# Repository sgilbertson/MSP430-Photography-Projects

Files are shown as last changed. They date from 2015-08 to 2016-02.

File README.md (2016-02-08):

# MSP430-Photography-Projects
Personal MSP430 projects, mainly photography-related

Here will place source code for some of my personal MSP430 microcontroller projects, mainly related to photography.

They're not designed for general use, but if you're working with MSP430 processors perhaps you'll find some of the material helpful or interesting.

Pololu DRV8825 Adjustment
=========================

See [https://www.pololu.com/product/2133]

Procedure:
 * Install jumper pulling M0,M1,M2 all low, for full stepping, not micro-stepping
 * Do not connect a motor
 * Clip the red lead of a voltmeter to a small screwdriver
 * Clip the black lead to ground
 * Apply power
 * Adjust the trimpot on the DRV8825 until the voltmeter reads half the motor amps rating

For example, if the motor is rated for 1A, adjust until the meter reads 0.5V.

Sample Motors
-------------

These are some motors I found in nearby surplus stores.

Japan Servo KP35M2-035
 * 37 ohms
 * Internet sources suggest 500mA, implying 0.5*37=18.5V -- tune to 250mV
 * 1.8° per pulse (200 pulses per rev), but testing suggests 4x that -- 1Hz ~50 seconds per rev, 200H ~4rev/sec
 * Runs OK on 12V around 250mA
 * Wdg1 = blue/red, Wdg2 = white/yellow

Litton-Clifton Precision 11-SHBX-51KT H347
 * 16 Ohms
 * 0.312A -- tune to 161mV
 * 0.312*16=5V
 * 1.8° per pulse

Small geared motor ABYJ28-5V or 24BYJ28-5V
 * 10x gear-down
 * Therefore 0.18°/pulse
 * 70 ohms, 5V, so 5/70=71.4mA -- tune to 36mV, or use 5V supply and tune high
 * Loads of torque at 5V up to about 100Hz (5 seconds per rev)
 * Won't start above 150Hz.
 * Wdg1 = blue/yellow, Wdg2 = orange/pink

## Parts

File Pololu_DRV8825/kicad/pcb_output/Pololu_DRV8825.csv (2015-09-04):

Id | Designator | Package | Quantity | Designation | Supplier and ref
1 | BT1 | Pin_Header_Straight_1x02 | 1 | Battery Pack
2 | C1,C2 | C_Disc_D6_P5 | 2 | 0.1uf
3 | C3 | C_Disc_D3_P2.5 | 1 | 2.2uf
4 | C4,C5 | C_Radial_D5_L6_P2.5 | 2 | 100uf
5 | D1,D2 | LED-3MM | 2 | LED
6 | J1,J2 | Pin_Header_Straight_1x02 | 2 | CONN_01X02
7 | P1,P2 | Pin_Header_Straight_1x10 | 2 | CONN_01X10
8 | P3,P4 | Pin_Header_Straight_2x10 | 2 | CONN_02X10
9 | P5,P6 | Pin_Header_Straight_1x04 | 2 | CONN_01X04
10 | R1,R2 | Resistor_Horizontal_RM15mm | 2 | 470
11 | R3 | Resistor_Horizontal_RM15mm | 1 | 10k
12 | U1 | DIP-20_W7.62mm | 1 | MSP430G2553IN20
13 | U2 | TO-92_Inline_Narrow_Oval | 1 | LM2931Z-3.3/5.0
14 | U3,U4 | DIP-16_W12.7mm | 2 | Pololu_DRV8825

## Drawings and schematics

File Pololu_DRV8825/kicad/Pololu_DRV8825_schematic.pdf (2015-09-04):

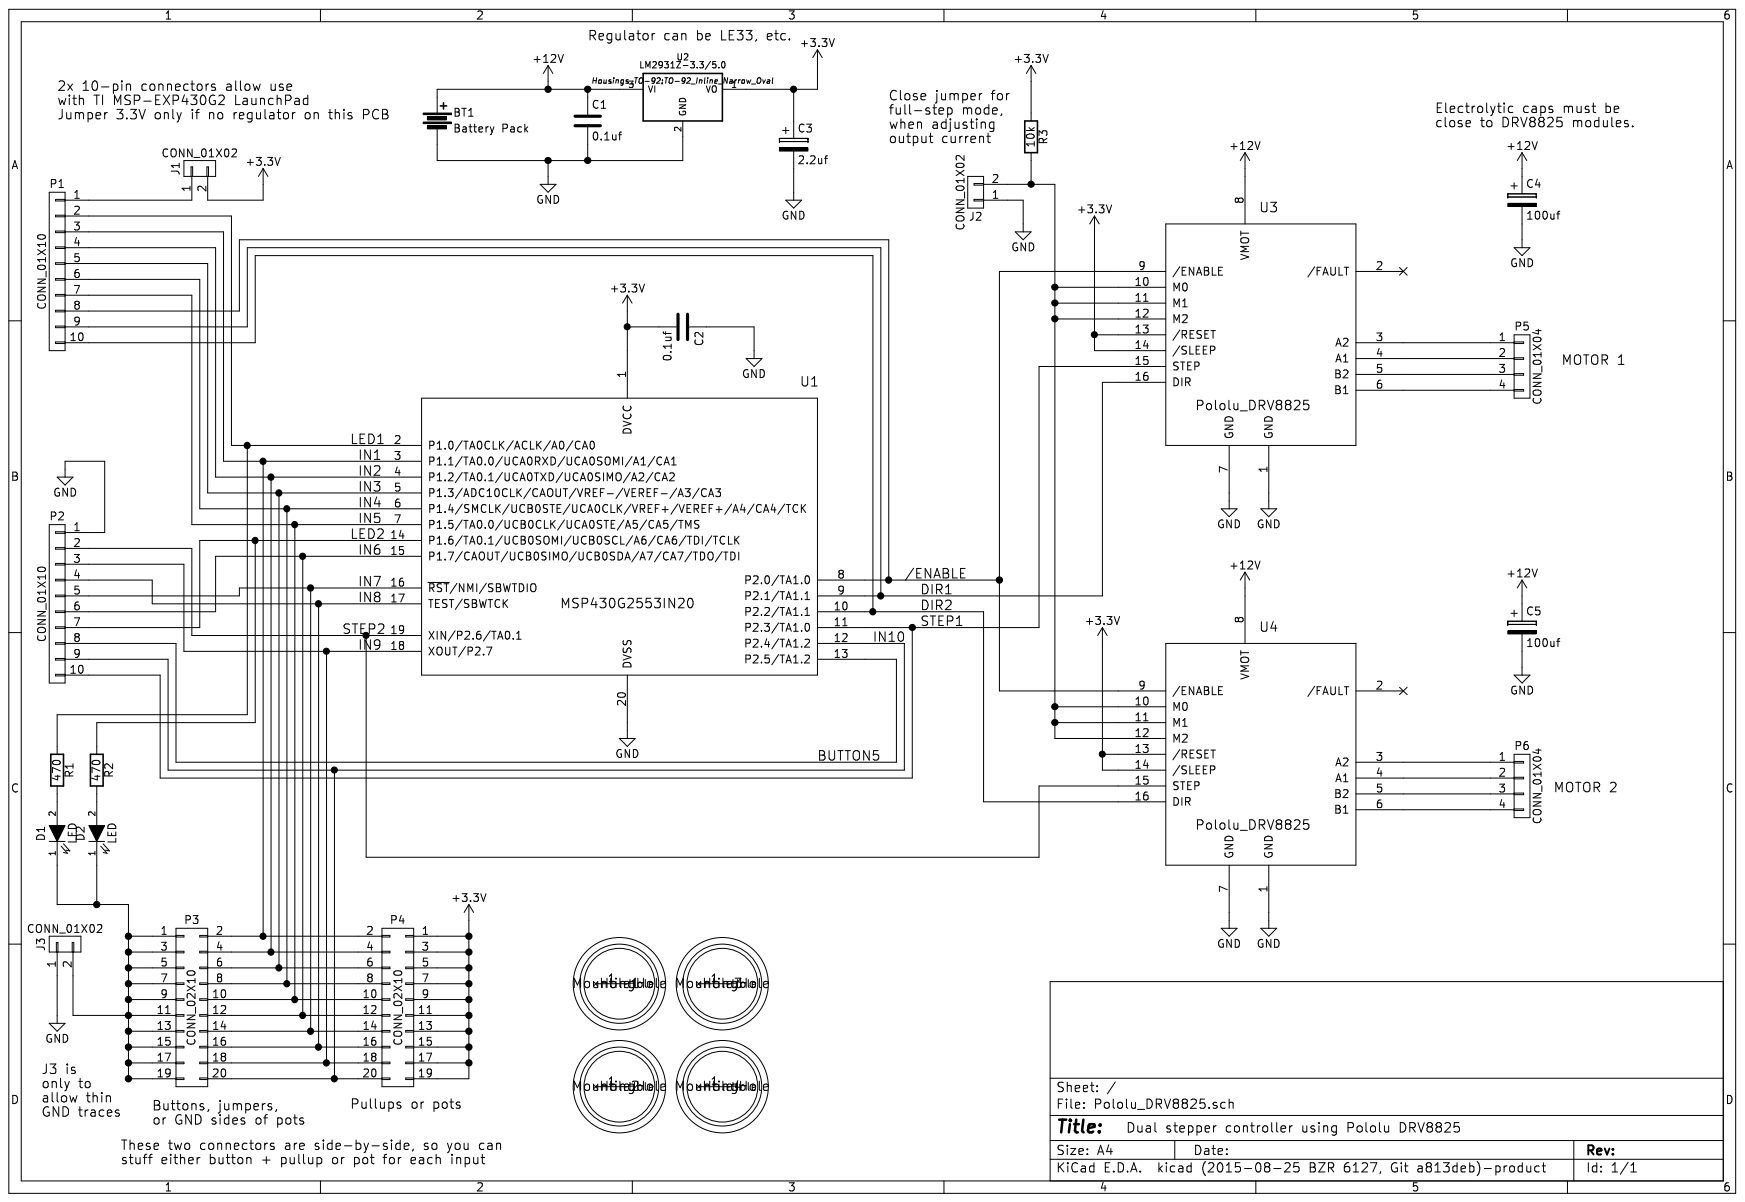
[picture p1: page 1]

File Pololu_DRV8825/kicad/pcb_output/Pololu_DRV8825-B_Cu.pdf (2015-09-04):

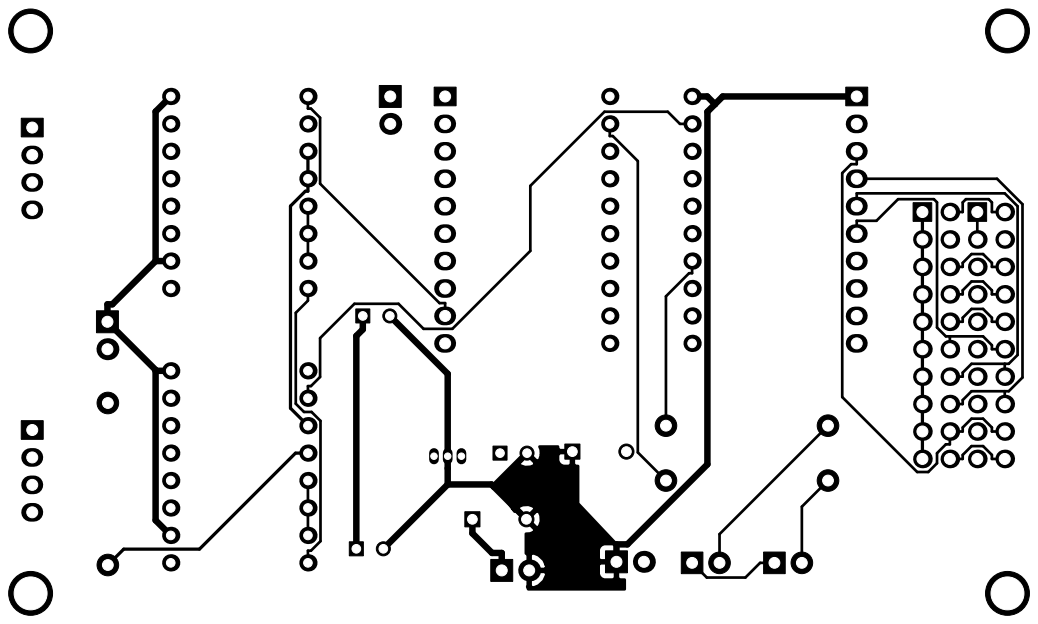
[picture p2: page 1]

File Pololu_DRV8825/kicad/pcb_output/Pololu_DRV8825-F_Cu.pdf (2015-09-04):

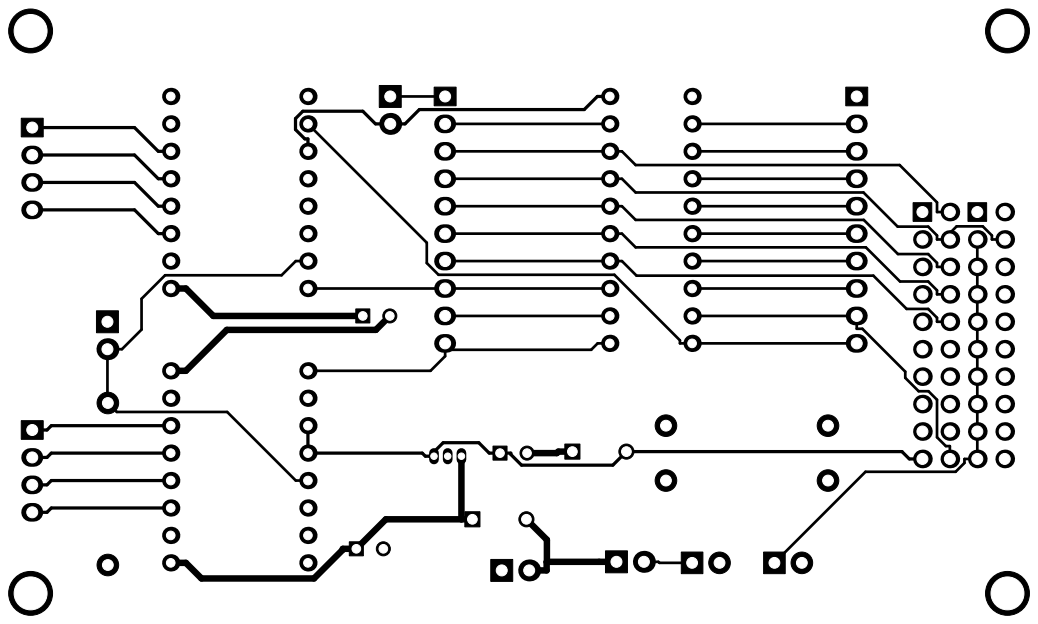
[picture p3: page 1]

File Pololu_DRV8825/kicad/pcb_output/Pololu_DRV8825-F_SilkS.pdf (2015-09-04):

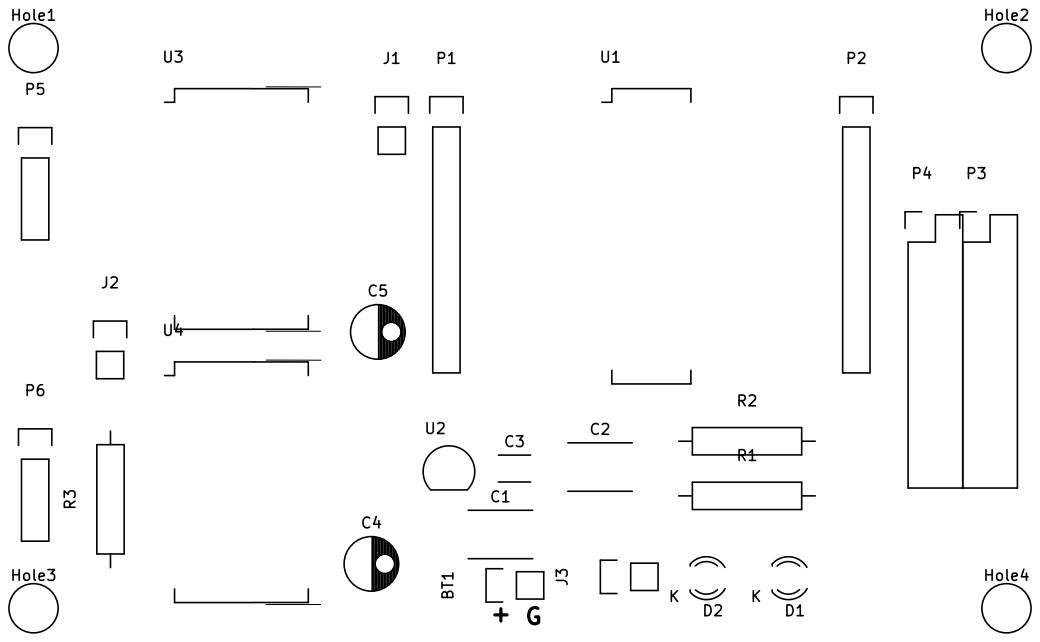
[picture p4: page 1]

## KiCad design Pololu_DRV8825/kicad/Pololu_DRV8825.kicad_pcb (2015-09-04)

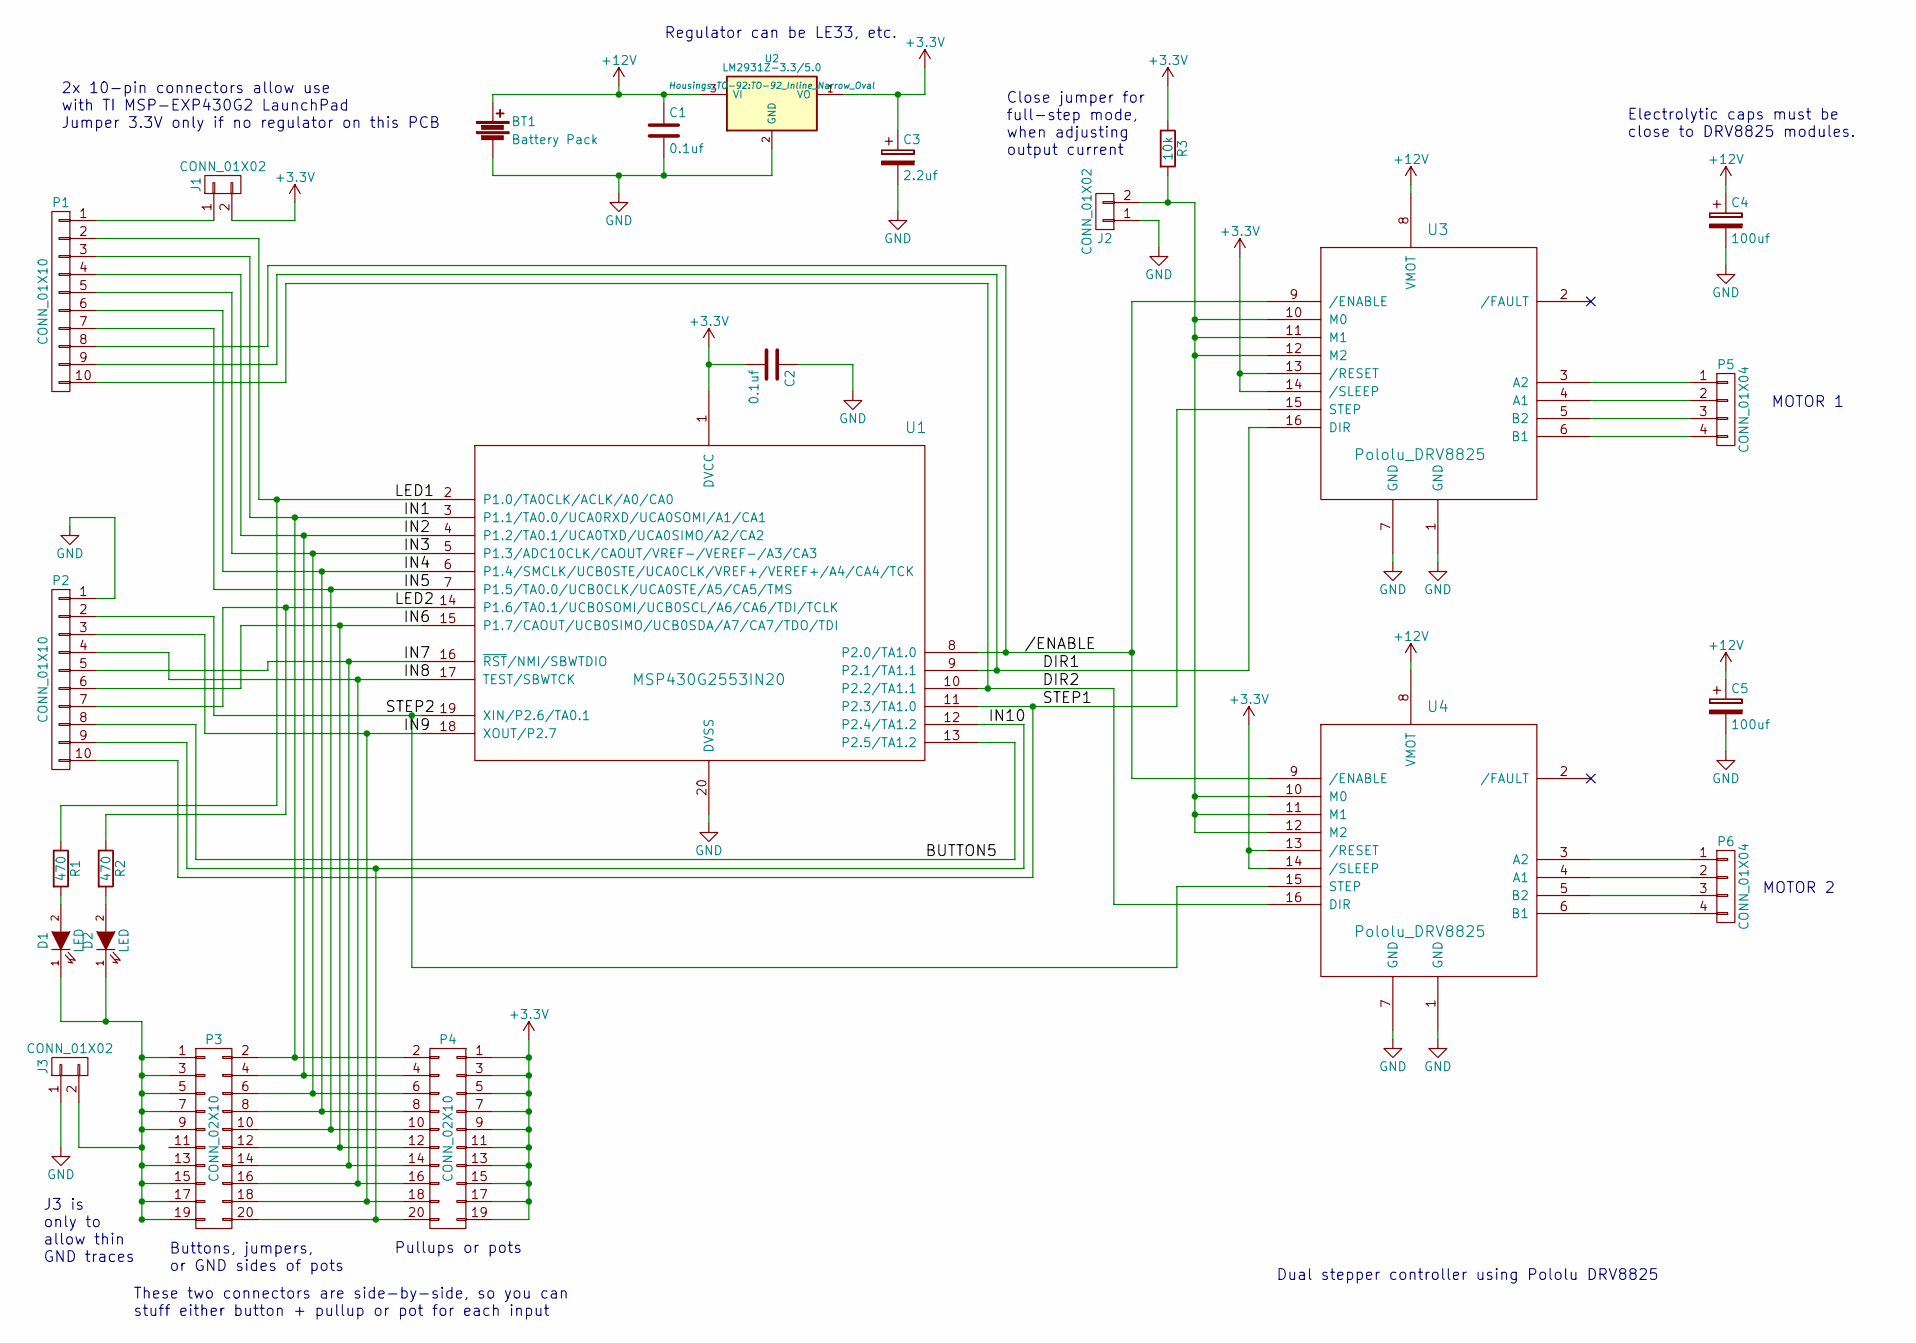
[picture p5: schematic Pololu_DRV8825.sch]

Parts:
BT1: Battery Pack; Pin_Header_Straight_1x02
C1, C2: 0.1uf; C_Disc_D6_P5
C3: 2.2uf; C_Disc_D3_P2.5
C4, C5: 100uf; C_Radial_D5_L6_P2.5
D1, D2: LED; LED-3MM
J1, J2, J3: CONN_01X02; Pin_Header_Straight_1x02
P1, P2: CONN_01X10; Pin_Header_Straight_1x10
P3, P4: CONN_02X10; Pin_Header_Straight_2x10
P5, P6: CONN_01X04; Pin_Header_Straight_1x04
R1, R2: 470; Resistor_Horizontal_RM15mm
R3: 10k; Resistor_Horizontal_RM15mm
U1: MSP430G2553IN20; DIP-20_W7.62mm
U2: LM2931Z-3.3/5.0; TO-92_Inline_Narrow_Oval
U3, U4: Pololu_DRV8825; DIP-16_W12.7mm

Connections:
+3V3: C2.2, C3.1, J1.2, P4.1, P4.3, P4.5, P4.7, P4.9, P4.11, P4.13, P4.15, P4.17, P4.19, R3.1, U1.1 (DVCC), U2.1 (VO), U3.13 (/RESET), U3.14 (/SLEEP), U4.13 (/RESET), U4.14 (/SLEEP)
+12V: BT1.1, C1.1, C4.1, C5.1, U2.3 (VI), U3.8 (VMOT), U4.8 (VMOT)
//ENABLE: P1.8, U1.8 (P2.0/TA1.0), U3.9 (/ENABLE), U4.9 (/ENABLE)
/BUTTON5: P2.8, U1.13 (P2.5/TA1.2)
/DIR1: P1.9, U1.9 (P2.1/TA1.1), U3.16 (DIR)
/DIR2: P1.10, U1.10 (P2.2/TA1.1), U4.16 (DIR)
/IN1: P1.3, P3.2, P4.2, U1.3 (P1.1/TA0.0/UCA0RXD/UCA0SOMI/A1/CA1)
/IN2: P1.4, P3.4, P4.4, U1.4 (P1.2/TA0.1/UCA0TXD/UCA0SIMO/A2/CA2)
/IN3: P1.5, P3.6, P4.6, U1.5 (P1.3/ADC10CLK/CAOUT/VREF-/VEREF-/A3/CA3)
/IN4: P1.6, P3.8, P4.8, U1.6 (P1.4/SMCLK/UCB0STE/UCA0CLK/VREF+/VEREF+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)
/IN5: P1.7, P3.10, P4.10, U1.7 (P1.5/TA0.0/UCB0CLK/UCA0STE/A5/CA5/TMS)
/IN6: P2.6, P3.12, P4.12, U1.15 (P1.7/CAOUT/UCB0SIMO/UCB0SDA/A7/CA7/TDO/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)
/IN7: P2.5, P3.14, P4.14, U1.16 (~RST~/NMI/SBWTDIO)
/IN8: P2.4, P3.16, P4.16, U1.17 (TEST/SBWTCK)
/IN9: P2.3, P3.18, P4.18, U1.18 (XOUT/P2.7)
/IN10: P2.9, P3.20, P4.20, U1.12 (P2.4/TA1.2)
/LED1: P1.2, R1.1, U1.2 (P1.0/TA0CLK/ACLK/A0/CA0)
/LED2: P2.7, R2.1, U1.14 (P1.6/TA0.1/UCB0SOMI/UCB0SCL/A6/CA6/TDI/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)
/STEP1: P2.10, U1.11 (P2.3/TA1.0), U3.15 (STEP)
/STEP2: P2.2, U1.19 (XIN/P2.6/TA0.1), U4.15 (STEP)
GND: BT1.2, C1.2, C2.1, C3.2, C4.2, C5.2, J2.1, J3.1, P2.1, U1.20 (DVSS), U2.2 (GND), U3.1 (GND), U3.7 (GND), U4.1 (GND), U4.7 (GND)
unnamed: D1.1 (K), D2.1 (K), J3.2, P3.1, P3.3, P3.5, P3.7, P3.9, P3.13, P3.15, P3.17, P3.19
unnamed: D1.2 (A), R1.2
unnamed: D2.2 (A), R2.2
unnamed: J1.1, P1.1
unnamed: J2.2, R3.2, U3.10 (M0), U3.11 (M1), U3.12 (M2), U4.10 (M0), U4.11 (M1), U4.12 (M2)
unnamed: P5.1, U3.3 (A2)
unnamed: P5.2, U3.4 (A1)
unnamed: P5.3, U3.5 (B2)
unnamed: P5.4, U3.6 (B1)
unnamed: P6.1, U4.3 (A2)
unnamed: P6.2, U4.4 (A1)
unnamed: P6.3, U4.5 (B2)
unnamed: P6.4, U4.6 (B1)

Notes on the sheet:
Dual stepper controller using Pololu DRV8825
2x 10-pin connectors allow use with TI MSP-EXP430G2 LaunchPad Jumper 3.3V only if no regulator on this PCB
Regulator can be LE33, etc.
Electrolytic caps must be close to DRV8825 modules.
Close jumper for full-step mode, when adjusting output current
MOTOR 1
MOTOR 2
Buttons, jumpers, or GND sides of pots
Pullups or pots
These two connectors are side-by-side, so you can stuff either button + pullup or pot for each input
J3 is only to allow thin GND traces

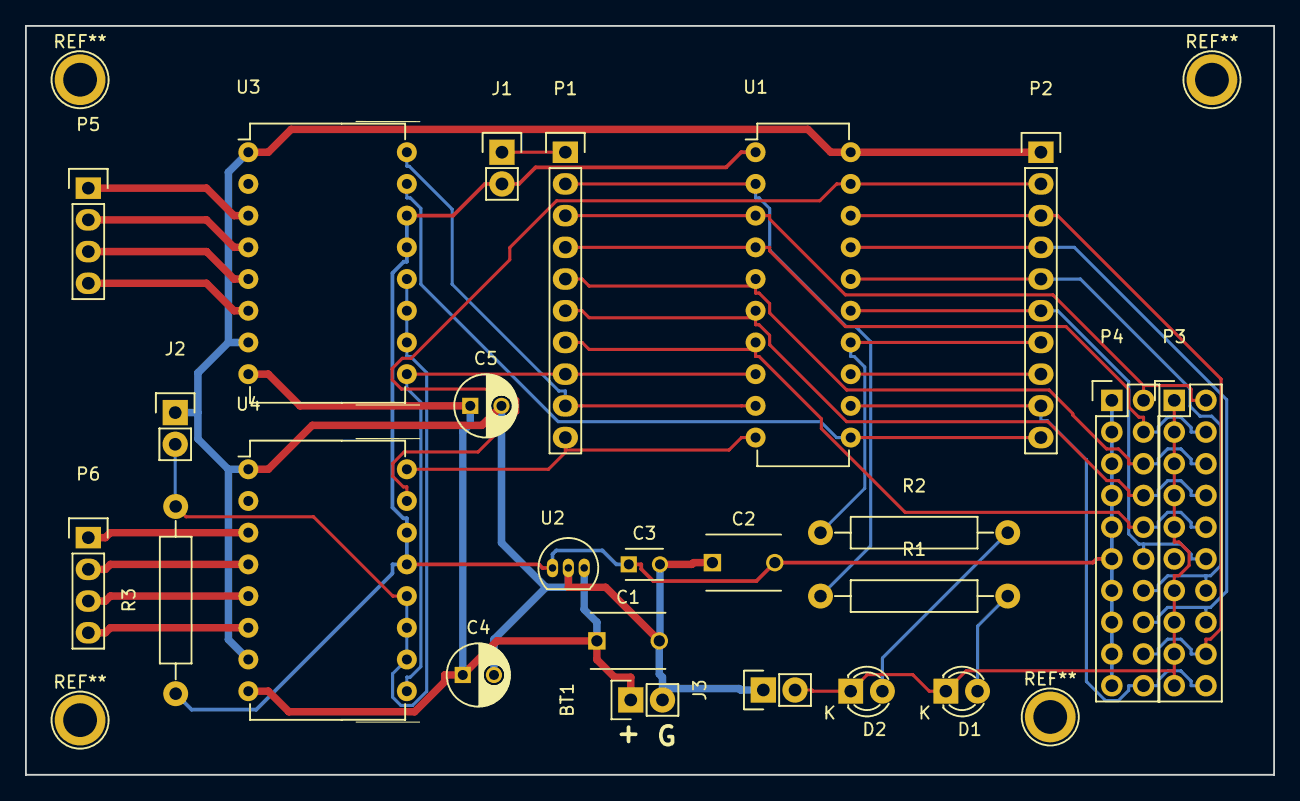
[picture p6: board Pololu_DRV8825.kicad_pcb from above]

Board: 2 copper layers, 100.0 x 60.0 mm, 24 parts (0 on the bottom side), 34 nets.

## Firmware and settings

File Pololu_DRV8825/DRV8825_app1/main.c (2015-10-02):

#include "msp430G2553.h"

/* DRV8825_app1 - Stepper motor driver for a motion time-lapse rig, using Pololu DRV8825 boards.
 *
 * Method:
 * Periodic interrupt occurs at four times the full step rate.
 * ISR toggles output pins to make two squarewaves 90° out of phase.
 *
 * Stepper motor output connections:
 *  - P2.0 = /ENABLE for both drivers
 *  - P2.1 = Motor 1 DIR
 *  - P2.5 = Motor 2 DIR
 *  - P2.3 = Motor 1 STEP
 *  - P2.6 = Motor 2 STEP
 *
 * LEDs, which mirror A+/B+
 *  - P1.0 LED 1 (same as on Launchpad)
 *  - P1.6 LED 2 (same as on Launchpad)
 *
 *  Speed control
 *   - A1 = potentiometer - forward speed (adjust by holding down forward button)
 *   - A2 = potentiometer - reverse speed (adjust by holding down reverse button)
 *
 *  Buttons (active low)
 *   - P1.3 = forward
 *   - P1.4 = reverse
 *   - P1.5 = stop -- can connect in parallel with a microswitch for a stop limit
 *
 */

// Stepper motor connection definitions
#define STEPPER_DISABLE BIT0
#define STEPPER_1_DIR BIT1
#define STEPPER_2_DIR BIT5
#define STEPPER_1_STEP BIT3
#define STEPPER_2_STEP BIT6
#define STEPPER_ALL_OUTPUTS (STEPPER_DISABLE + STEPPER_1_DIR + STEPPER_2_DIR + STEPPER_1_STEP + STEPPER_2_STEP)
#define STEPPER_ALL_STEP_BITS (STEPPER_1_STEP + STEPPER_2_STEP)

#define STEPPER_DIR P2DIR
#define STEPPER_OUT P2OUT

// Button port/bit definitions
#define BUTTON_PORT P1IN
#define BUTTON_FORWARD BIT3
#define BUTTON_REVERSE BIT4
#define BUTTON_STOP BIT5
#define BUTTON_ALL_BITS (BUTTON_FORWARD|BUTTON_REVERSE|BUTTON_STOP)

typedef enum
{
	RUNSTATE_OFF,
	RUNSTATE_FORWARD,
	RUNSTATE_REVERSE
} RunningState;


// LEDs
#define     LED1                  BIT0
#define     LED2                  BIT6
#define     LED_ALL               (LED1|LED2)
#define     LED_DIR               P1DIR
#define     LED_OUT               P1OUT

#define APPROX_CLOCK_HZ 1107754
#define MICROSTEP_RATIO 32	// DRV8825 does a 32-point sinewave for micro-stepping
#define MIN_STEP_HZ ((unsigned short)((APPROX_CLOCK_HZ+32767)/65535))
#define MAX_STEP_HZ (MICROSTEP_RATIO*300)	// experimentally derived for a particular 0.312mA motor

volatile short irqcount0 = 0;
volatile unsigned short step_interval = APPROX_CLOCK_HZ / (MICROSTEP_RATIO*20); // start at 20Hz, which is 5 steps per second
volatile unsigned short stepperBits = STEPPER_DISABLE | STEPPER_2_DIR;
volatile unsigned short countPer100ms = 0;
volatile unsigned short countPerButtonStateChange = 0;
volatile RunningState runningState = RUNSTATE_OFF;
volatile int adc_buffer[10] = {0};
void main(void)
{
	volatile unsigned short lastCountPer100ms = countPer100ms;
	volatile unsigned short lastCountPerButtonStateChange = countPerButtonStateChange;
	unsigned short forwardStepInterval = step_interval;
	unsigned short reverseStepInterval = step_interval;
	RunningState adjustingState = RUNSTATE_OFF;
	RunningState nextAdjustingState = RUNSTATE_OFF;
	WDTCTL = WDTPW + WDTHOLD;  // Stop WDT

	LED_DIR |= LED_ALL;
	LED_OUT &= ~LED_ALL;
	STEPPER_DIR |= STEPPER_ALL_OUTPUTS;
	STEPPER_OUT &= ~STEPPER_ALL_OUTPUTS;

	// Set up A/D converter for speed-control potentiometer
	ADC10CTL0 = ADC10SHT_2 + ADC10ON + MSC; // ADC10 enabled, multiple conversions, 16 x ADC10CLKs, interrupts disabled
	ADC10CTL1 = CONSEQ_1 + INCH_2;                       // DTC transfer, input A2,A1
	ADC10AE0 |= (BIT1 + BIT2);                         // PA.1 & PA.2 ADC option select (not digital I/O)
	ADC10DTC0 = 0;	// one-block mode (sample each input once, then stop)
	ADC10DTC1 = 2;	// 2 conversions

	// Set up a timer interrupt for stepper PWM generation
//	BCSCTL1 |= DIVA_1;                        // ACLK/2
//	BCSCTL3 |= LFXT1S_2;                      // ACLK = VLO

	TA0CCTL0 = CCIE;                             // CCR0 interrupt enabled
	TA0CCR0 = 50000;
	TA0CTL = TASSEL_2 + MC_2;                  // SMCLK, contmode
	
	// Set up another timer interrupt, for general timing operations
	TA1CCTL0 = CCIE;                             // CCR0 interrupt enabled
	TA1CCR0 = 50000;
	TA1CTL = TASSEL_2 + MC_2;                  // SMCLK, contmode

	// Buttons are inputs
	P1DIR &= ~BUTTON_ALL_BITS;
	// Enbable an interrupt whenever the state of a button changes
	P1IE |= BUTTON_ALL_BITS;
	P1IES = 0;	// interrupt on falling edges -- gets adjusted in ISR
	P1IFG &= ~BUTTON_ALL_BITS;

	__enable_interrupt();
	while(1)
	{
		__bis_SR_register(LPM0_bits + GIE);          // LPM0 with interrupts enabled
		// We get here when the A/D conversion ends after each 100ms interrupt...
		if (lastCountPer100ms != countPer100ms)
		{
			if (adjustingState != RUNSTATE_OFF)
			{
				int adChannel = ((adjustingState == RUNSTATE_FORWARD) ? 0 : 1);
				unsigned short adcValue = adc_buffer[adChannel];	// 0..1023
				// The idea here is to set step_interval to 65535 if adcValue is very low, and to some
				// small value if it's high. The small value is selected so that it isn't too fast for the motor.
				unsigned short hz = ((unsigned long)adcValue*(MAX_STEP_HZ-MIN_STEP_HZ))/1023 + MIN_STEP_HZ;
				unsigned long adcReciprocal = ((unsigned long)APPROX_CLOCK_HZ) / hz;
				step_interval = (unsigned short)(adcReciprocal&0xFFFF);
				if (adjustingState == RUNSTATE_FORWARD)
					forwardStepInterval = step_interval;
				else
					reverseStepInterval = step_interval;
			}
			if (runningState == RUNSTATE_FORWARD)
				step_interval = forwardStepInterval;
			else
				step_interval = reverseStepInterval;
			adjustingState = nextAdjustingState;	// button must be held down >100ms to adjust speed
			lastCountPer100ms = countPer100ms;
			// Start the next conversion, with transfers going to adc_buffer
			ADC10CTL0 &= ~ENC;				// Disable Conversion
		    while (ADC10CTL1 & BUSY);		// Wait if ADC10 busy
		    ADC10CTL1 = CONSEQ_1 + INCH_2;	// FIXME: are we supposed to have to do this every time?
		    ADC10SA = (int)&adc_buffer[0];
			ADC10CTL0 |= ENC + ADC10SC;             // Sampling and conversion start for next interval
		}
		// ... or when a button input has changed state ...
		if (lastCountPerButtonStateChange != countPerButtonStateChange)
		{
			if (!(BUTTON_PORT & BUTTON_STOP))
			{
				nextAdjustingState = adjustingState = RUNSTATE_OFF;
				runningState = RUNSTATE_OFF;
				STEPPER_OUT |= STEPPER_DISABLE;
			}
			else if (!(BUTTON_PORT & BUTTON_FORWARD))
			{
				nextAdjustingState = RUNSTATE_FORWARD;
				runningState = RUNSTATE_FORWARD;
				STEPPER_OUT |= STEPPER_1_DIR;
				STEPPER_OUT &= ~STEPPER_DISABLE;
				ADC10CTL1 = INCH_1;                       // input A1
			}
			else if (!(BUTTON_PORT & BUTTON_REVERSE))
			{
				nextAdjustingState = RUNSTATE_REVERSE;
				runningState = RUNSTATE_REVERSE;
				STEPPER_OUT &= ~STEPPER_1_DIR;
				STEPPER_OUT &= ~STEPPER_DISABLE;
				ADC10CTL1 = INCH_2;                       // input A2
			}
			else
			{
				nextAdjustingState = adjustingState = RUNSTATE_OFF;
			}
			lastCountPerButtonStateChange = countPerButtonStateChange;
		}
	}
}

// Port 1 interrupt service routine -- fires when a button is pressed or released
#pragma vector=PORT1_VECTOR
__interrupt void Port_1(void)
{
	countPerButtonStateChange++;
	P1IFG &= ~BUTTON_ALL_BITS;	// clear the interrupt condition
	P1IES = BUTTON_PORT & BUTTON_ALL_BITS;	// look for opposite transitions
	__bic_SR_register_on_exit(CPUOFF);	// wake up the main loop
}

// Timer A0 interrupt service routine
// Updates the step PWM outputs.
#pragma vector=TIMER0_A0_VECTOR
__interrupt void Timer_A0 (void)
{
	irqcount0++;
	switch(irqcount0&8)	// Slow down the output by a factor of 8, to make up for timer being too fast for good time-lapse motion
	{
	case 0:
		stepperBits = STEPPER_1_STEP;
		break;
	default:
	case 1:
		stepperBits = 0;
		break;
	}
	if (runningState != RUNSTATE_OFF)
	{
		STEPPER_OUT = (STEPPER_OUT & ~STEPPER_ALL_STEP_BITS) | stepperBits;
	}
	// LEDs indicate the speed and direction
	if (runningState == RUNSTATE_OFF)
		LED_OUT = (LED_OUT&~LED_ALL) | LED1 | LED2;	// both LEDs on
	if (STEPPER_OUT & STEPPER_1_DIR)
		LED_OUT = (LED_OUT&~LED_ALL) | ((stepperBits&STEPPER_1_STEP)?LED1:0);	// one LED flashing
	else
		LED_OUT = (LED_OUT&~LED_ALL) | ((stepperBits&STEPPER_1_STEP)?LED2:0);	// other LED flashing
	TA0CCR0 += step_interval;                            // Add Offset to CCR0 to set time of next interrupt
}

// Timer A1 interrupt service routine
// Fires at a fixed rate for general timing operations
// The ISR starts an ADC conversion and icrements a counter.
// The ADC interrupt will wake up the main loop
#pragma vector=TIMER1_A0_VECTOR
__interrupt void Timer_A1 (void)
{
	countPer100ms++;
	TA1CCR0 += (APPROX_CLOCK_HZ/10);	// enter this ISR ten times per second
	__bic_SR_register_on_exit(CPUOFF);	// wake up the main loop
}

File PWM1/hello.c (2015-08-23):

#include "msp430G2553.h"

/* PWM inverter to drive 24V AC motor for time-lapse rig
 * 
 * Connections:
 *  - P2.2 drives one MOSFET
 *  - P2.4 drives the other MOSFET
 *  - P1.0 LED 1 (same as on Launchpad) 
 *  - P1.6 LED 2 (same as on Launchpad) 
 */

#define     LED1                  BIT0
#define     LED2                  BIT6
#define     LED_DIR               P1DIR
#define     LED_OUT               P1OUT

#define APPROX_CLOCK_HZ 1107754
#define PWM_FREQUENCY 60
#define PWM_PERIOD (APPROX_CLOCK_HZ/50)
#define PWM_25_PERCENT (PWM_PERIOD/4)
#define PWM_75_PERCENT ((PWM_PERIOD*3)/4)

short irqcount = 0;
 
void main(void)
{
	WDTCTL = WDTPW + WDTHOLD;  // Stop WDT

	LED_DIR |= LED1 + LED2;                          
	LED_OUT &= ~(LED1 + LED2);  

	// Set up a timer interrupt
//	BCSCTL1 |= DIVA_1;                        // ACLK/2
//	BCSCTL3 |= LFXT1S_2;                      // ACLK = VLO

	TA0CCTL0 = CCIE;                             // CCR0 interrupt enabled
	TA0CCR0 = 50000;
	TA0CTL = TASSEL_2 + MC_2;                  // SMCLK, contmode
	
//	TA0CCR0 = 1200;                            //   
//	TA0CTL = TASSEL_1 | MC_1;                  // TACLK = SMCLK, Up mode.  
//	TA0CCTL1 = CCIE + OUTMOD_3;                // TACCTL1 Capture Compare
//	TA0CCR1 = 600;  
 
	// Two channels of PWM output from Timer1_A3
	P2DIR |= (BIT2 | BIT4);             // P2.2, P2.4 to output
	P2SEL |= (BIT2 | BIT4);             // P2.2 to TA1.1, P2.4 to TA1.2

	TA1CCR0 = PWM_PERIOD-1;             // PWM Period
	TA1CCTL1 = OUTMOD_6;          // CCR1 toggle/set -- output on in high part of triangle
	TA1CCR1 = PWM_75_PERCENT;                // CCR1 PWM duty cycle
	TA1CCTL2 = OUTMOD_2;          // CCR2 toggle/reset -- output on in low part of triangle
	TA1CCR2 = PWM_25_PERCENT;                // CCR2 PWM duty cycle
	TA1CTL = TASSEL_2 + MC_3;     // SMCLK, up/down mode
 
	__enable_interrupt();
	__bis_SR_register(LPM0_bits + GIE);          // LPM0 with interrupts enabled
}

// Timer A0 interrupt service routine
#pragma vector=TIMER0_A0_VECTOR
__interrupt void Timer_A0 (void)
{
	irqcount++;
	LED_OUT ^= ((irqcount&4)?LED1:0) | ((irqcount&6)?LED2:0); 
	/*
	if (LED_OUT | LED1)
		LED_OUT = (LED_OUT ^ LED2) && ~LED1;
	else
		LED_OUT |= LED1;
	*/
	TA0CCR0 += 50000;                            // Add Offset to CCR0             
}

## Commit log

2015-08-23 Initial commit of PWM1 project, which aims to drive an AC motor using a pair of power MOSFETs
2015-08-23 Initial commit of Stepper 1 project, which aims to control a stepper motor for motion time-lapse photography. Initially, the code is copied from PWM1.
2015-08-23 Stepper 1: Initial implementation of bipolar output to L293D or similar driver chip using 4 output pins, with the A+ and B+ states reflected on the LEDs.
2015-08-24 Stepper1 typo fix -- was writing step signals to the wrong port.
    [main.c]
2015-08-24 Stepper1: Added variable speed using a potentiometer
    Potentiometer connects to the AD1 pin.
    Speed is limited to 500Hz ISR rate maximum.
    Minimum is roughly interval=65535
2015-09-04 Initial commit of dual Pololu DRV8825 stepper driver board
    [Pololu_DRV8825.kicad_pcb, Pololu_DRV8825.sch]
2015-09-04 DRV8825 - parts placed
    [Pololu_DRV8825.kicad_pcb, Pololu_DRV8825.sch]
2015-09-04 DRV8825 first routed board with mounting holes
    [Pololu_DRV8825.kicad_pcb, Pololu_DRV8825.sch]
2015-09-04 Ready for first manufacturing run
    [Pololu_DRV8825.csv, Pololu_DRV8825.dsn, Pololu_DRV8825.sch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]
2015-09-11 Copied Stepper1 software project, to start DRV8825_app1
    [Pololu_DRV8825-B_Cu.gbr, Pololu_DRV8825-B_SilkS.gbr, Pololu_DRV8825-F_Cu.gbr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]
2015-09-11 Hacked together enough code to get some pulses going to the driver for motor 1. Pot on A1 controls the speed.
2015-09-26 Initial implementation of forward/reverse/stop buttons
    [main.c]
2015-09-30 attempting to get direction buttons and dual speed pots working
2015-10-02 Got forward/reverse speed control apparently working, with buttons for forward, reverse and stop. Holding down the forward or reverse button obtains the speed setting from its respective ADC input.
    [main.c]
2016-02-08 Added documentation of current-limit adjustment and some specific motors.
